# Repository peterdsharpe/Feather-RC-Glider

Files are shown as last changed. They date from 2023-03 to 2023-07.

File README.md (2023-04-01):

# Feather

by Peter Sharpe

-----

**Feather is a 1-meter-wingspan RC glider with an all-up weight of around 60 grams.**

It's optimized to achieve the lowest possible sink-rate in still-air cruise flight, in order to maximize flight duration during calm early mornings and its ability to exploit low-altitude thermals for lift.

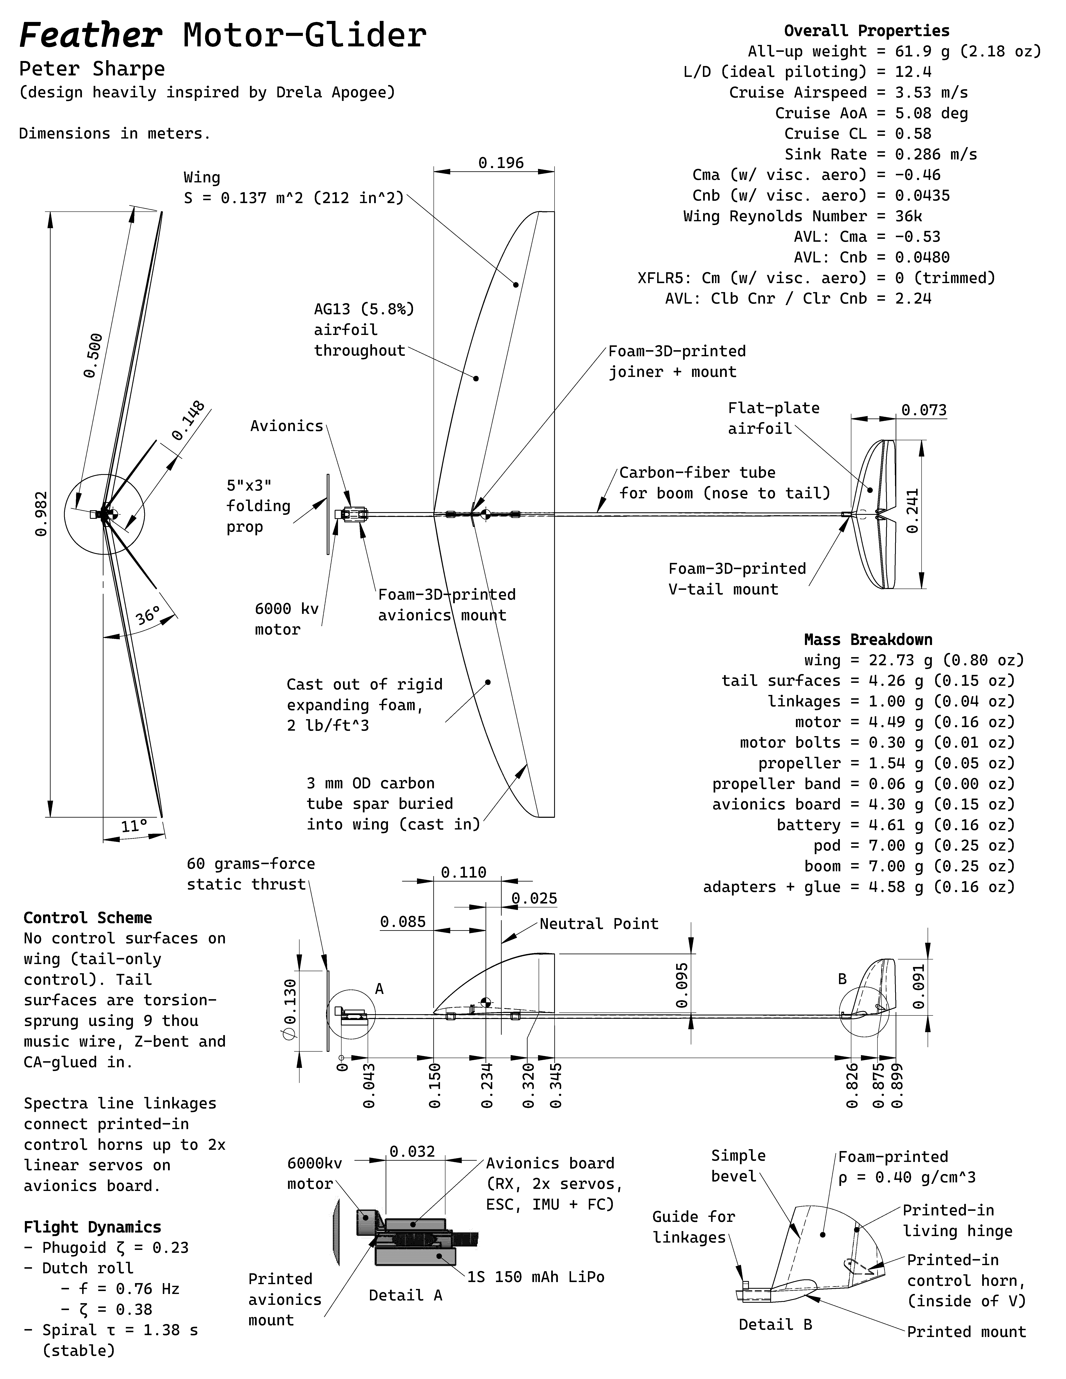
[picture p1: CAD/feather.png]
three-view


([PDF](./CAD/feather.pdf))

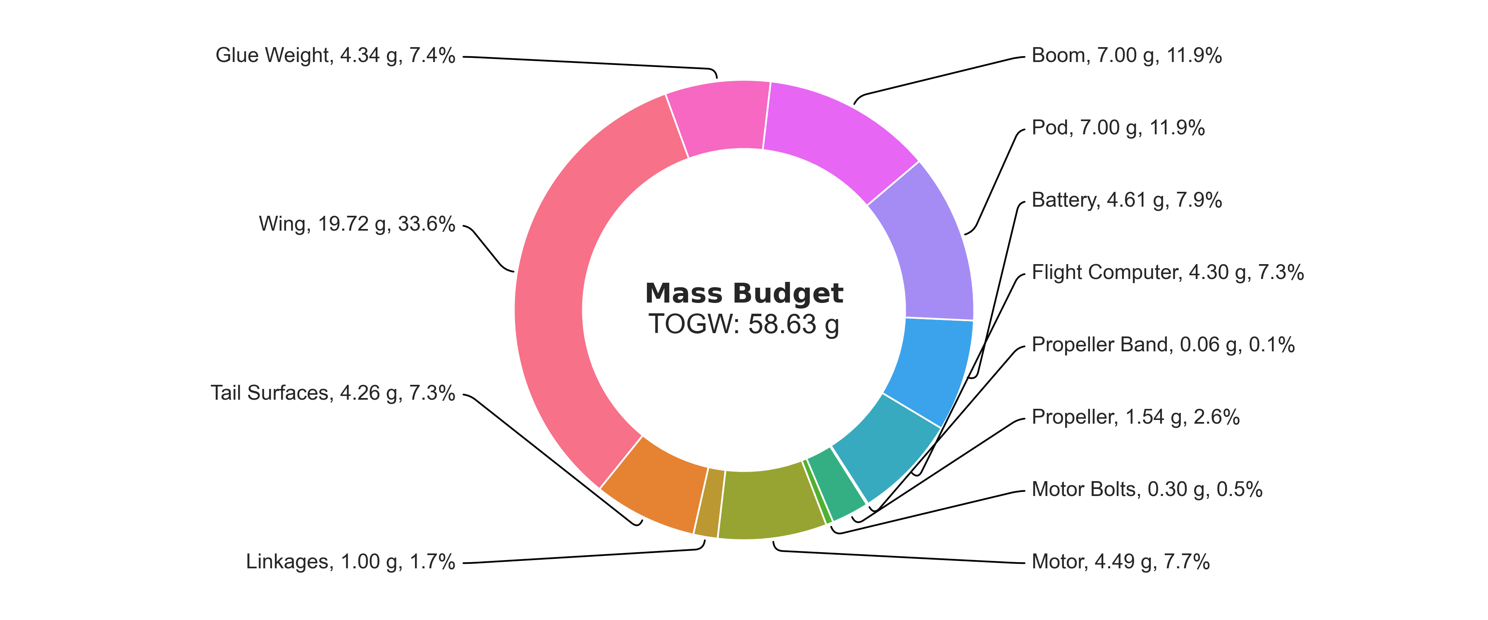
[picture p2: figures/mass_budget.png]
mass-budget


## Conceptual Design Considerations

Remote-controlled gliders in this size range typically fall into one of two categories:

- Hand-launch gliders (HLG), which are thrown "javelin-style" (like a football, but without the spiral)
- Discus-launch gliders (DLG), which are launched by holding the glider by a wingtip and spinning your whole body in a circle (about the airplane's yaw axis), then releasing.

Discus-launch gliders can [achieve some truly unbelievable launch altitudes](https://www.youtube.com/watch?v=onFAnlK0M_4&t=24s) (up to 70 meters, for the pros). This has several key benefits:

1. Higher launch altitude means longer flight times, assuming a constant sink-rate.
2. Higher launch altitude means more time to find thermals.
3. At higher altitude, thermals are typically wider and have longer durations before dissipating.
4. At higher altitude, thermals are typically stronger in magnitude. This is because the ground effectively acts as a no-penetration boundary condition for the 3D wind field, so getting farther away from the ground increases updraft and downdraft magnitudes. (Note: this is only true at relatively low altitudes, roughly <1 km, for complicated reasons that are beyond scope here...)

But, discus-launch gliders have some significant drawbacks, all of which are associated with their violent launch conditions:

1. The wing structural weight must be much higher (sometimes double what they would be for hand-launch gliders) to support the high launch forces, which can sometimes be as much as 30 G.
2. Tailbooms must be much stiffer (read: heavier) to support the high yaw moment during launch as the airplane goes from spinning to straight flight.
3. The design space for tail geometries is constrained by the need to minimize fuselage boom torsion. For example, a V-tail is typically undesirable, because the side force on the tail surfaces would cause excessive boom torsion. This results in lost performance at cruise.
4. Vertical stabilizers typically use asymmetric airfoils in order to deal with the high vertical stabilizer lift coefficient during launch de-rotation. This results in lost performance at cruise.

Basically, DLGs launch higher than HLGs, but they are heavier and less efficient at cruise.

-----

Feather aims to do something else, to combine the best parts of a DLG with the best parts of a HLG. 

In recent years, electric powertrains have gotten so lightweight and integrated that it may be possible to achieve the same launch altitude as a DLG, but without any of the launch-force constraints.

Specifically, Feather uses a BLDC motor + propeller to get up to altitude, and then shuts off its powertrain to glide - it's your typical motor glider, but at an unprecedentedly-small scale.

Feather is essentially built around [this powertrain](https://www.buzzardmodels.com/4gram1spro-brick), which is a pretty magical piece of technology. In short:

For 15.3 grams, you get:

- A 1S 3.7V 150mAh LiPo battery
- A 5-amp ESC for a BLDC motor
- An EX1103-6000kv BLDC motor
- A 5x3 propeller
- Two BM5320 linear servos
- An IMU + flight controller for PID stabilization to the servos
- A FrSky-compatible RC receiver

which is pretty nuts. Given that the battery + receiver + 2 servos of a typical 1-meter DLG would weigh ~20 grams, we're essentially getting an entire powertrain for free, plus an additional 5 grams weight savings.

The lack of a launch means we can build the main structural elements (wing and tailboom) much, much lighter, leading to **Feather's overall all-up weight of around 60 grams**. This compares to typical 1-meter-wingspan DLGs, the lightest of which weigh around 100 grams (assuming highest-end modern molded composite construction, etc.).

## Detailed Design Considerations

Section to be written...

## Build Progress

All components manufactured, except for the wing itself. 

### Wing

The manufacturing process for wings cast out of foam is a bit of a black art, so a lot of experimentation is needed to get it right:

#### Attempt 1

Under-expanded, although foam is rigid, the wing is very light, and the surface finish is promising. Casting into a set of PETG 3d-printed molds, which are sanded to a 1000-grit finish (surprisingly, this only takes a few minutes with the right power tools!) and wax-coated.

Release was tough.

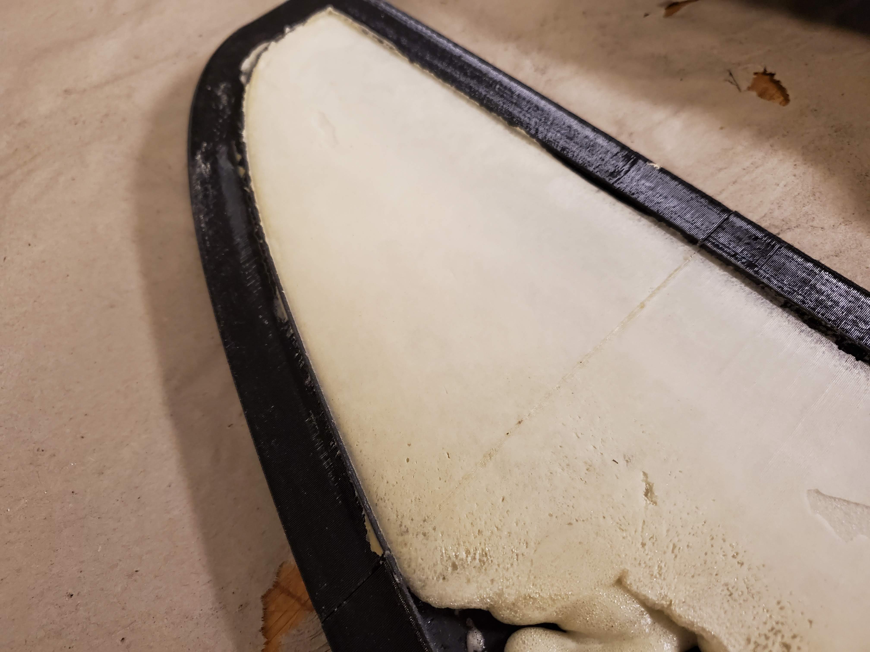
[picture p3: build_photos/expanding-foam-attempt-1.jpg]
wing-1


#### Attempt 2

In addition to wax, I also added PVA as a release agent for this attempt. That worked great.

Added more foam to prevent under-expansion, but I erred a bit on the opposite side. The force of the expanding foam was
so much that it forced the two halves of the mold apart (which was only held together by ~40 lbs of weights), resulting in the wrong outer mold line.

Surface finish is acceptable (would need some sanding). As a consequence of too much foam, the wing is a bit heavy (~35 grams). Quite stiff, though.

#### Attempt 3

To be done, but changes will include:
- Splitting the difference between the two foam amounts, to hopefully neither under- nor over-expand.
- Clamping the mold using C-clamps rather than weights, to prevent the mold from opening up in the event of over-expansion (there is a release hole in the mold).

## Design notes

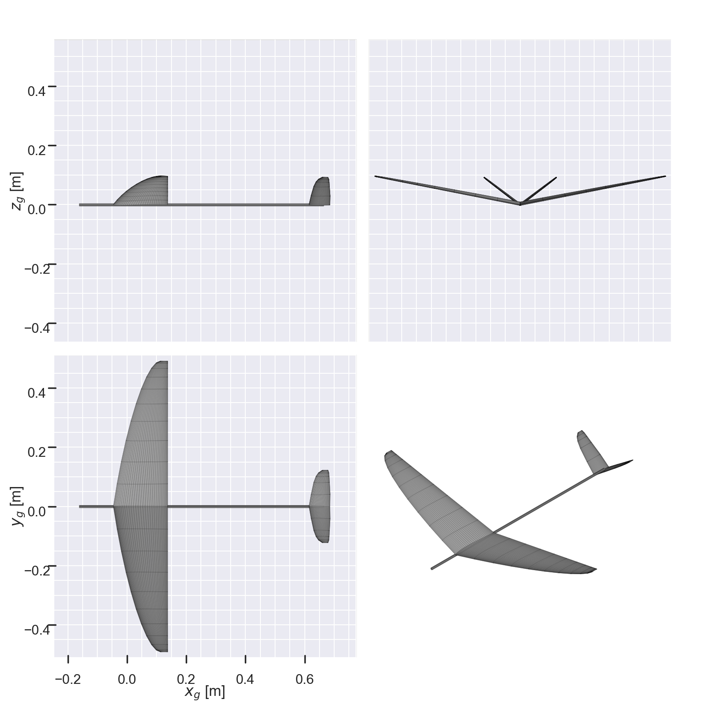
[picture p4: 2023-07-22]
figures/three_view.png

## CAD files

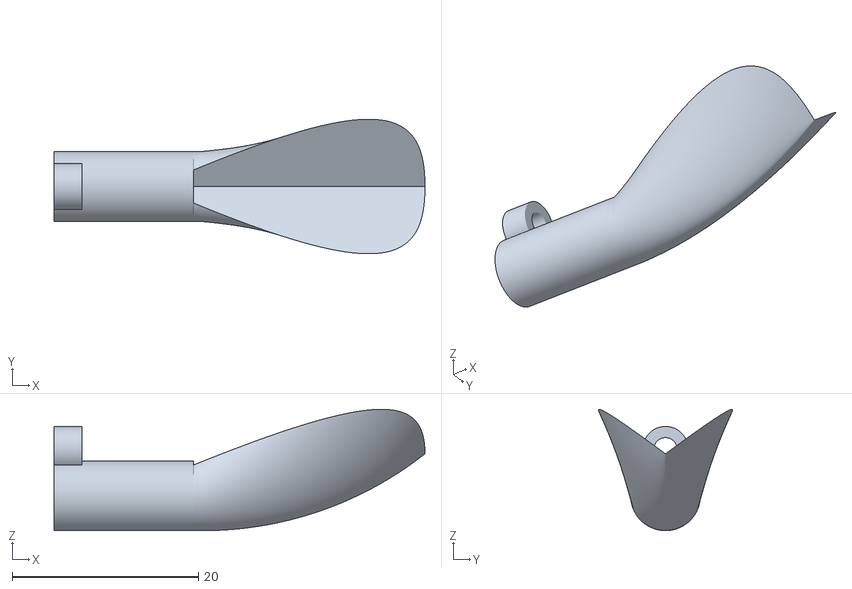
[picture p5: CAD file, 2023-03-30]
CAD/STLs/VTail Mount^feather-assembly.STL
39.9 x 14.5 x 13.0

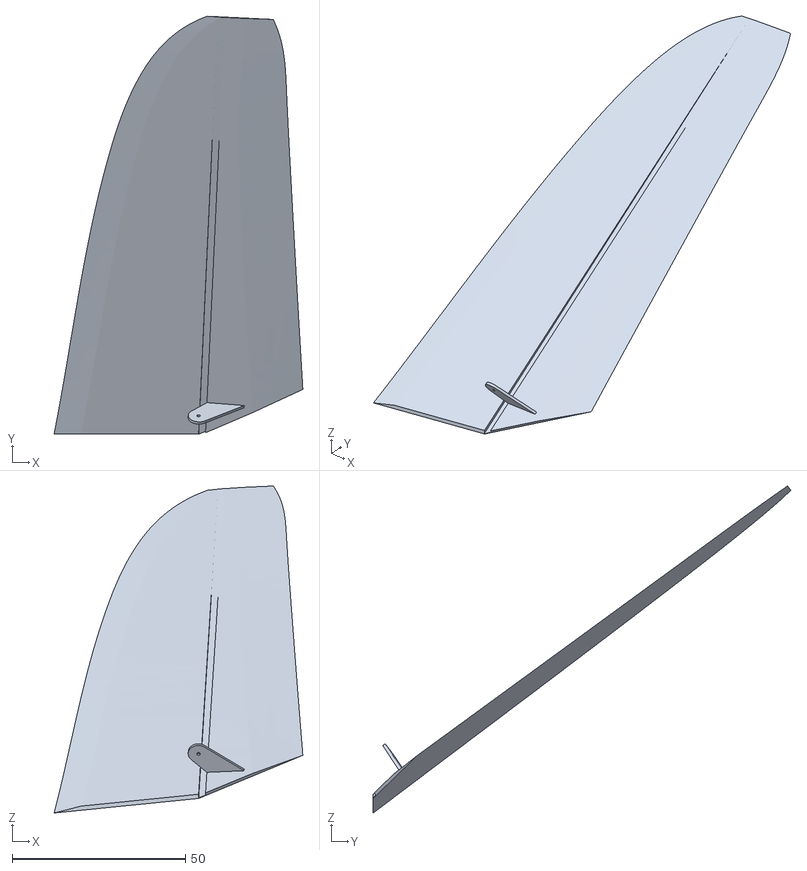
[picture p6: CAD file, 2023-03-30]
CAD/STLs/VTail^feather-assembly.STL
71.8 x 120.6 x 94.5

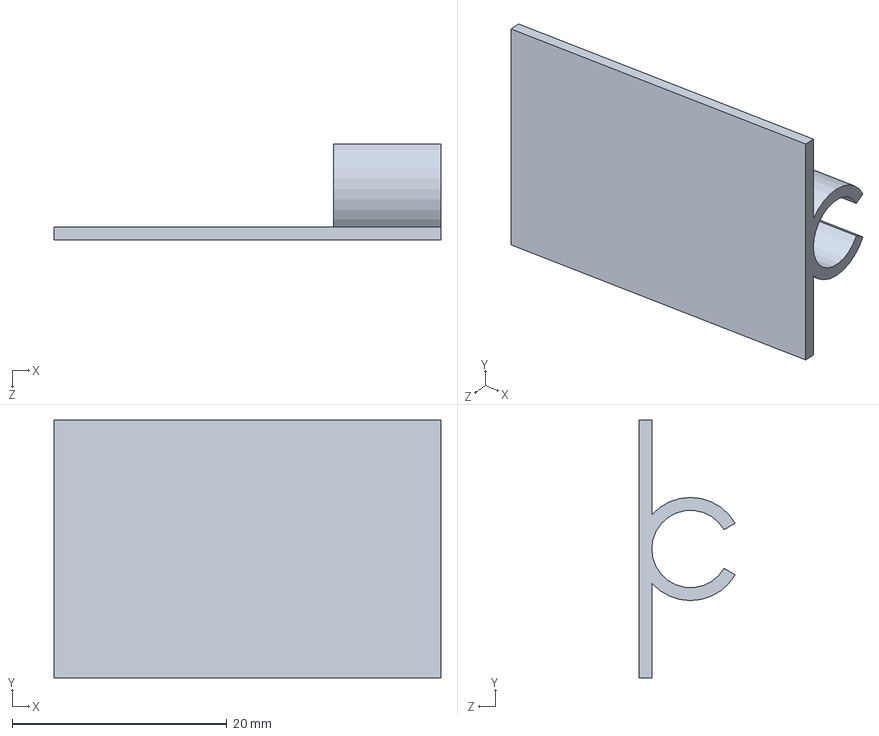
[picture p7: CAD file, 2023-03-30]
CAD/FC Mount.SLDPRT
36.0 x 24.0 x 8.96 mm

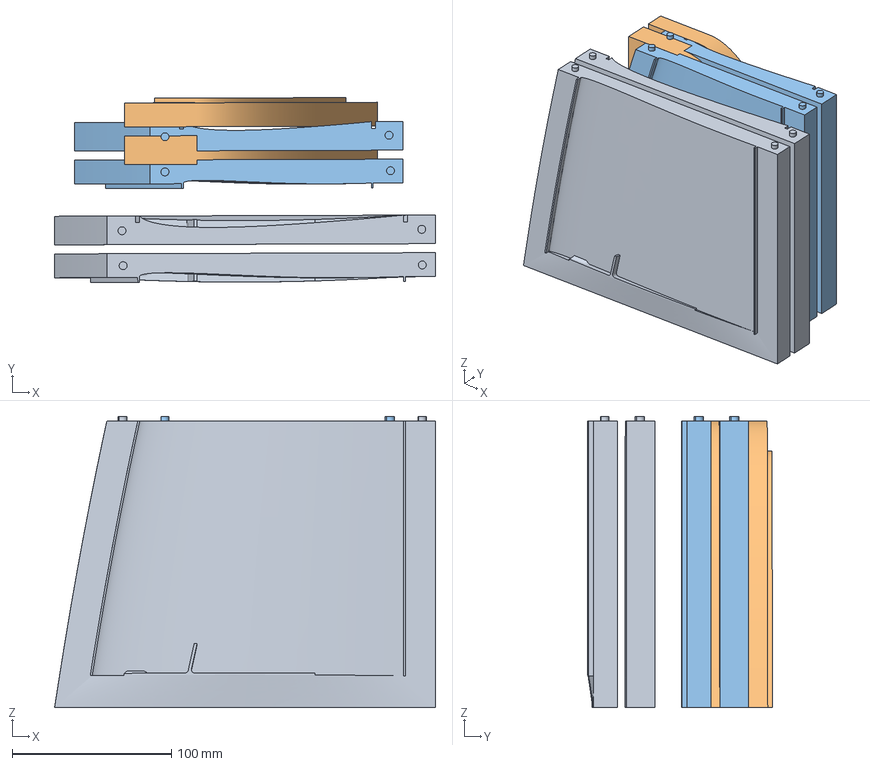
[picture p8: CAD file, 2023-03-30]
CAD/STLs/wing_molds.3mf
239.4 x 116.1 x 183.0 mm
wing_molds.STL x 3

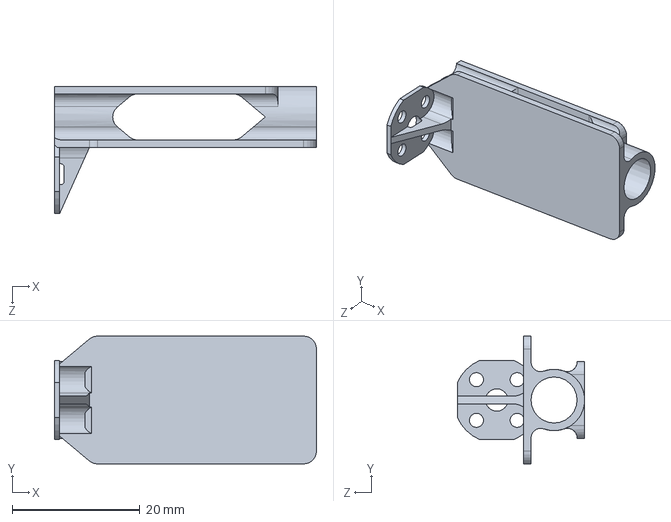
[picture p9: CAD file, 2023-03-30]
CAD/Motor Mount.SLDPRT
41.0 x 20.0 x 19.9 mm

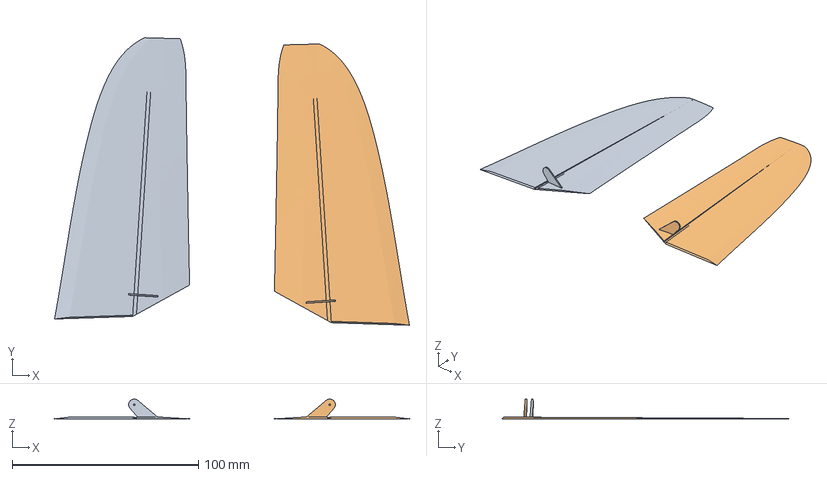
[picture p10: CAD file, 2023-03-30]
CAD/STLs/vtail.3mf
190.7 x 154.5 x 10.6 mm
VTail^feather-assembly.STL x 2

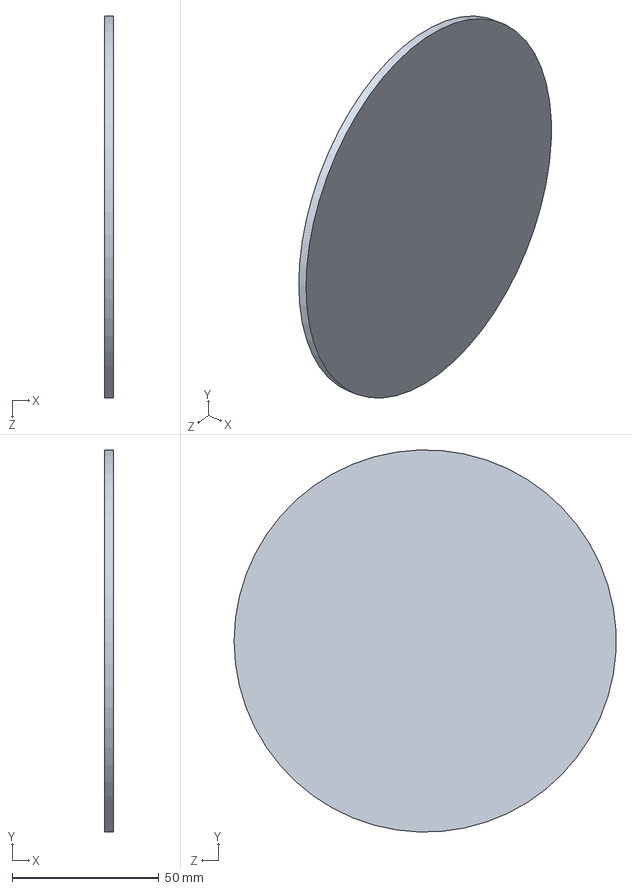
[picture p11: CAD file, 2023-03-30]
CAD/Prop.SLDPRT
3.00 x 129.9 x 129.9 mm

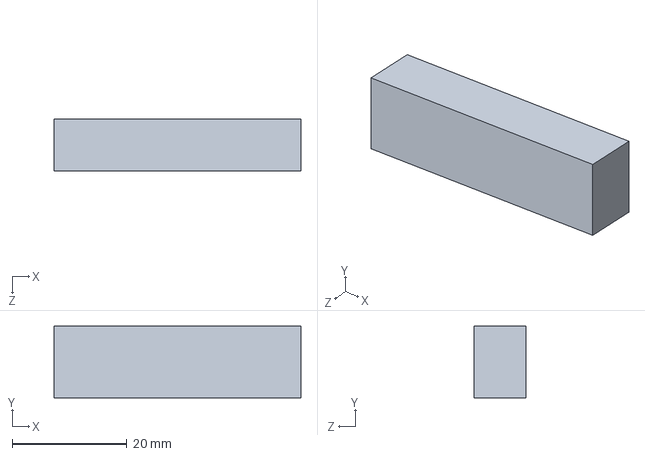
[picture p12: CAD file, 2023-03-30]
CAD/Battery.SLDPRT
43.0 x 12.5 x 9.00 mm

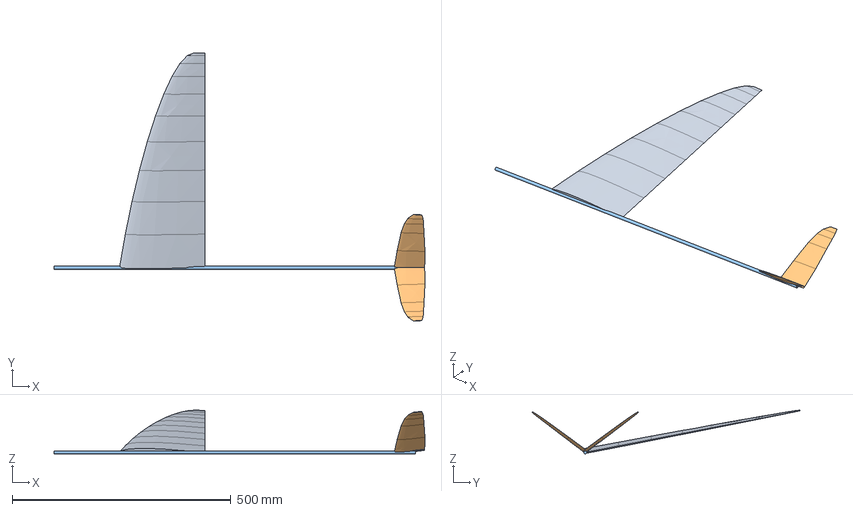
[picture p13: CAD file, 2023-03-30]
CAD/feather.step
847.5 x 612.9 x 100.1 mm

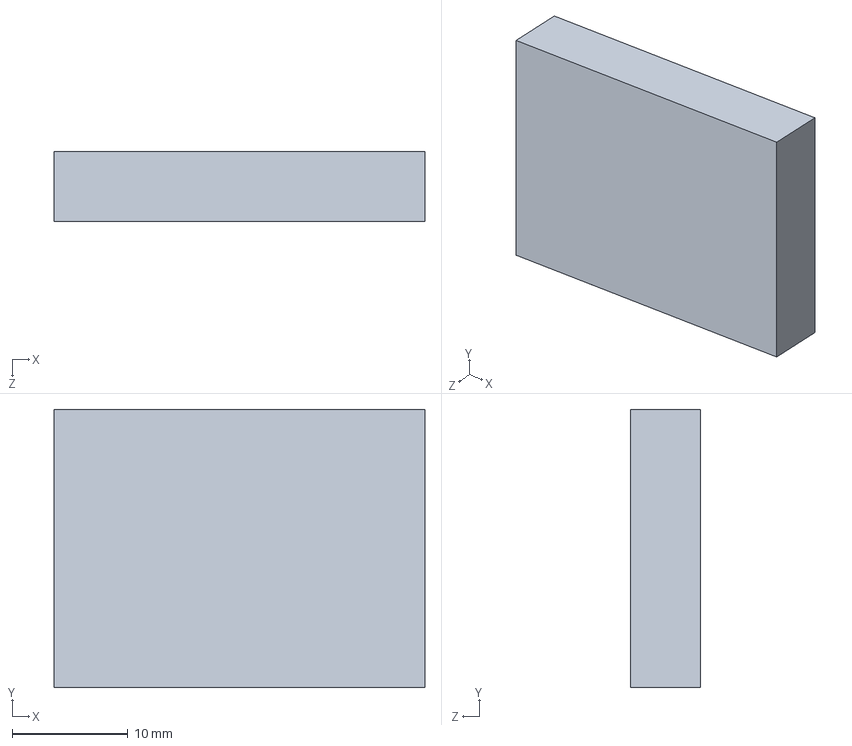
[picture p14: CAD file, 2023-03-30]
CAD/FC.SLDPRT
32.0 x 24.0 x 6.00 mm

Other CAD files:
CAD/Motor.SLDPRT
CAD/STLs/Motor Mount.STL
CAD/feather-assembly.SLDDRW

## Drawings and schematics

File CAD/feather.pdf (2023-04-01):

# Feather Motor-Glider

## Peter Sharpe

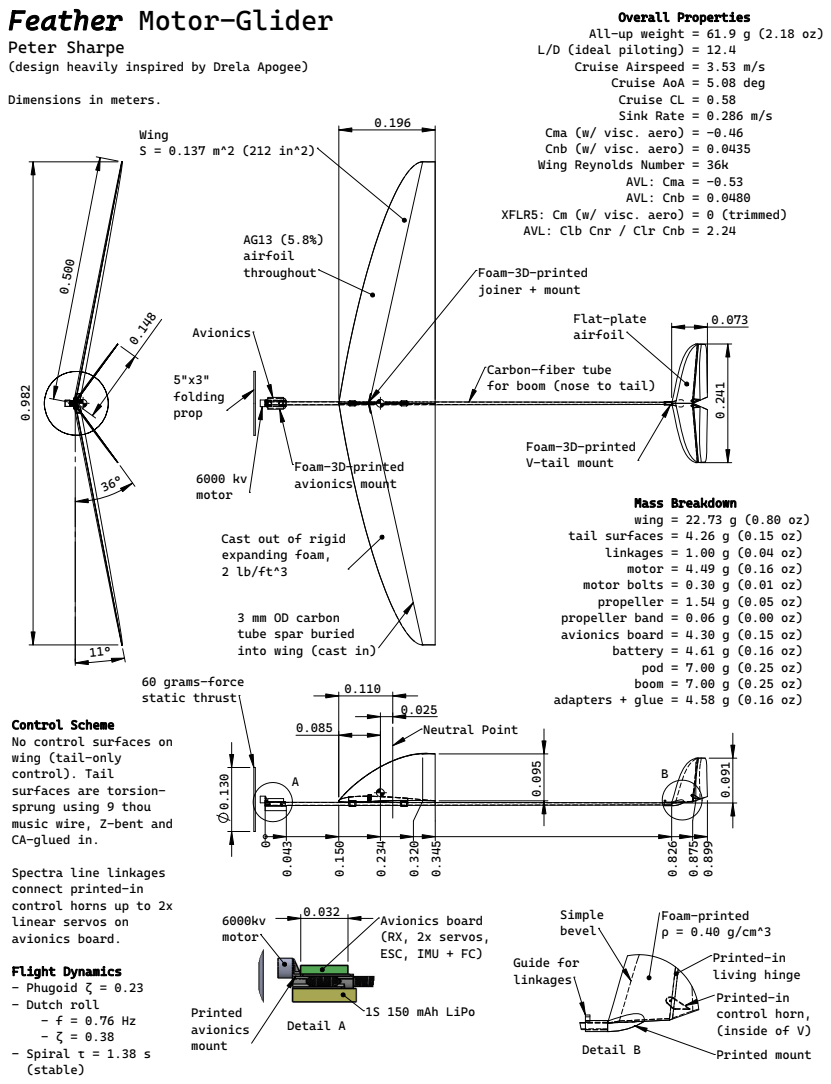
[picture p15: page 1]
airfoil; joiner + mount; Avionics; Wing; motor; Foam-3D-printed; avionics mount; Flat-plate; V-tail mount; throughout; Flight Dynamics - Phugoid ζ = 0.23 - Dutch roll - f = 0.76 Hz - ζ = 0.38 - Spiral τ = 1.38 s (stable); Mass Breakdown wing = 22.73 g (0.80 oz); battery = 4.61 g (0.16 oz) pod = 7.00 g (0.25 oz) boom = 7.00 g (0.25 oz); AVL: Cma = -0.53 AVL: Cnb = 0.0480; 1S 150 mAh LiPo; 6000kv motor; Detail A; Printed avionics mount; linkages; Printed mount; bevel; Printed-in living hinge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

Overall Properties
All-up weight = 61.9 g (2.18 oz)

L/D (ideal piloting) = 12.4
Cruise Airspeed = 3.53 m/s
Cruise AoA = 5.08 deg
Cruise CL = 0.58
Sink Rate = 0.286 m/s

(design heavily inspired by Drela Apogee)

Dimensions in meters.

Cma (w/ visc. aero) = -0.46
Cnb (w/ visc. aero) = 0.0435
Wing Reynolds Number = 36k

XFLR5: Cm (w/ visc. aero) = 0 (trimmed)
AVL: Clb Cnr / Clr Cnb = 2.24

Carbon-fiber tube

for boom (nose to tail) 5"x3"
folding
prop

Cast out of rigid
expanding foam,

tail surfaces = 4.26 g (0.15 oz)
linkages = 1.00 g (0.04 oz)
motor = 4.49 g (0.16 oz)

motor bolts = 0.30 g (0.01 oz)
propeller = 1.54 g (0.05 oz)
propeller band = 0.06 g (0.00 oz)
avionics board = 4.30 g (0.15 oz)

3 mm OD carbon
tube spar buried
into wing (cast in)

adapters + glue = 4.58 g (0.16 oz)

Control Scheme
No control surfaces on
wing (tail-only
control). Tail
surfaces are torsion-
sprung using 9 thou
music wire, Z-bent and
CA-glued in.

Spectra line linkages
connect printed-in
control horns up to 2x
linear servos on
avionics board.

Avionics board
(RX, 2x servos,
ESC, IMU + FC)

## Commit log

2023-03-30 Add CAD and XFLR files
    [Battery.SLDPRT, FC Mount.SLDPRT, FC.SLDPRT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]
2023-04-01 add drawing, update XFLR5, update SolidWorks. No airplane adjustments other than tail incidence tweak
    [feather-assembly.SLDDRW]
2023-04-01 add note on drawings about dimensions in meters
    [feather-assembly.SLDDRW]
2023-07-22 update solidworks drawing
    [feather-assembly.SLDDRW]
